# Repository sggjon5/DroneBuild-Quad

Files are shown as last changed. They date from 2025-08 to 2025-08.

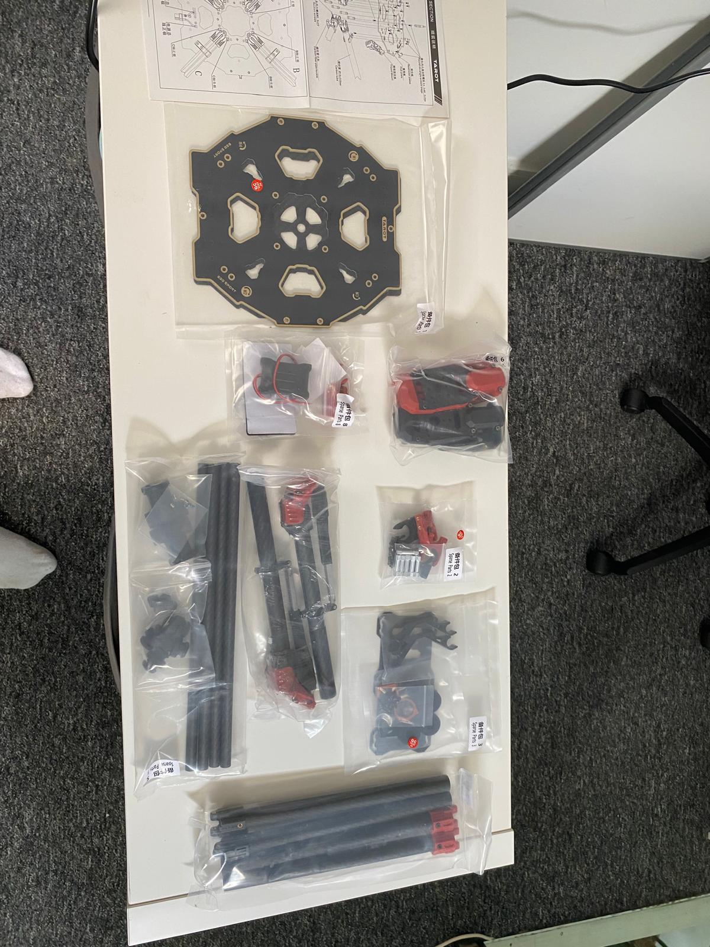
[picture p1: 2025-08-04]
media/images/frame_assembly/fame_box_component_bags.jpg

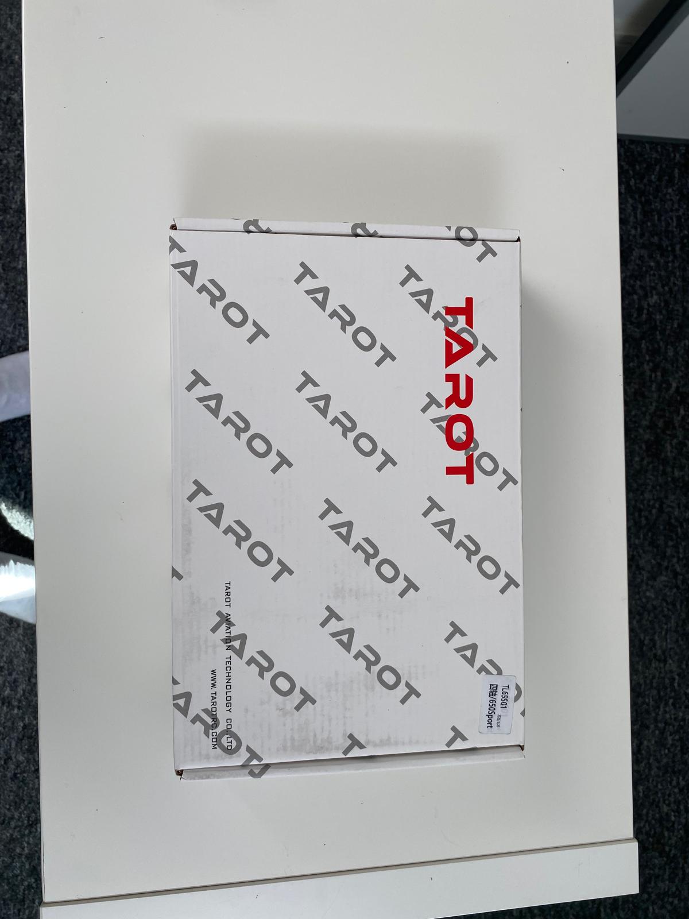
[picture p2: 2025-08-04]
media/images/frame_assembly/frame_box_closed.jpg

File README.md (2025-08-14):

# 🛠️ DroneBuild-Quad
Documenting a custom quadcopter build completed summer 2025.

hotshot

Intended to be comprehensive (but not too boring) and honest. Any questions, omissions or mistakes feel free to reach out. It has not been endorsed or sponsored by any of the products or sellers that I mention. If I have anything particular to say (good or bad) about an experience or product, it is likely included near to the section where it was utilised in the build process.

---

## 📑 Contents 

- [👋 Introduction](docs/01-introduction.md)
- [🧩Parts List](docs/02-parts-list.md)
- [🔨 Tools List](docs/02b-tools-list.md)
- [🏗️ Frame Assembly](docs/03-frame-assembly.md)
- [🪫 ESCs](docs/04-esc.md)
- [🧲 Motors](docs/05-motors.md)
- [📡 Telemetry](docs/06-telemetry.md)
- [🎮📻 Transmitter & Receiver](docs/07-transmitter-receiver.md)
- [🛰️ GPS](docs/08-gps.md)
- [💻 Software Configuration](docs/09-software-config.md)
- [✈️ Flight Testing](docs/10-flight-testing.md)

---

## 🎥 Demo Video
Please click the image below to view the drone in action. For some reasons Youtube has uploaded it as a short and I am unaware of how to change this. I am unable to upload the file to github as it is over the size limit. I have uploaded a couple of videos to a canva whiteboard that can be found [here](https://www.canva.com/design/DAGwCvz3RpU/Q3_VmZ7DQnh24HMWHGmF7A/view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). The quality should not be compressed in these

Maiden flight video (https://www.youtube.com/shorts/46lmEJWYgyI)

--- 

## 🚠 Cable/Wiring Diagram
Below is a schematic of the wiring within the quad. I feel compelled to say that it is in fact, (Not to scale).

It is an .svg file and therefore you should be able to download & zoom to read the small text notes scattered around it. 

Wiring Diagram

It does not yet include the companion computer, but I anticipate connecting this to the telem2 port of the flight controller. I have not yet decided how this will be powered.

This was made on a Canva whiteboard, as those who know me will be aware, I am a big advocate for Canva for all things presentation and design.

---

## 🤕 Mistakes

- Did not tell the vendor of the motors I was using when ordering the ESC, so had to buy a DATA LINK V2 to flash the firmware myself (~£150)
- ESCs are a bit big to run the cables through the motor arms so had to run them externally (still looks neat but less so than internal cabling) (no cost)
- Bought a wire stripper/cutter that is not very good at cutting and honestly surplus to requirements for a project of this scale... (~£25)
- Ordered the wrong XT60 pigtail (female) and soldered it to the drone, warranting either a replacement or a male to male XT60 converter (~£5)
- Did not apply threadlocker to my metal to metal connections initially (~£10)

---

## 🎉 Positive & Good Things

- The communication and fast delivery from all of the vendors (most notably 3DXR and FlyingTech) has been brilliant every time
- The soldering station is solid, does everything I would want it to and probably made my life a lot easier
- The top plate of the frame is a PDB, which I think is cool
- The battery charger did not break the bank, and it can be used as a bench DC power supply
- The build quality of the X18 transmitter feels very sturdy and good

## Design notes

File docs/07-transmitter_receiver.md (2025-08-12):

# 📻 🎮  Receiver and Transmitter 

- **Receiver** - FrSky ARCHER PLUS RS
- **Transmitter** - FrSky Tandem X18

I will provide info about the receiver, then transmitter, then the binding process and finally my configuration of mixes.

---

## 📻 Receiver
The receiver used for this build is the FrSky Archer Plus RS 2.4 GHz. This is an incredibly small and lightweight reciever weighing just over a gram. The datasheets spec it to be able to operate at >2km in good conditions and I found the whole registering and binding process very straight forward. [The datasheet](https://www.frsky-rc.com/wp-content/uploads/Downloads/Amanual/ARCHER%20PLUS%20RS%20RS%20Mini%20Manual.pdf) explains how to set up this receiever in a set of relativley short and easy steps.

The 'work' you have to do to get it ready for use is three solder joints. I used a servo cable (22 AWG) and soldered directly to the plated through holes on the board.

> [!TIP]
> Change your soldering iron tip from the gigantic one you probably used to do the ESC/PDB/Power, to a fine point one, these connections are very small.

The three connections you have to solder are as follows (colouring as a guideline only, but conforms to convention):

- Black - GND
- Red - VIN
- White - SBUS_OUT

  archer_plus_rs_pinout

 These three cables then go into a Servo connector and is connected to the "RC IN" pins on the flight controller (along the bottom edge of the orange+), with black corresponding to - and white corresponding to s.

reciever_soldered

> [!WARNING]
> **Do not stick this receiver to the frame using foam tape attached to the side with the button**. I did this and it literally pulled the button off so I had to spend 10 minutes reconstructing it with a pair of very fine tweezers to be able to bind the transmitter.

As can be seen in the above photo, the button is not actually attached anymore, this is because it was stuck to the foam tape I had used to mount it to the frame. I attached it to the top of the bottom plate when affixing it to the frame, on the back right hand side, with the antennas hanging out the side of the central body of the drone. As you can also (just about) see in the below image, the servo connector that is attached to the three cables that were soldered to the receiver, are connected to the RC IN port on the cube (furthest left rail on the bottom of the flight controller).

receiver_onboard

---

## 🎮 Transmitter

The transmitter used for this project was the FrSky Tandem X18 Dual Band transmitter. 

x18_transmitter

x18_transmitter_case

There is again, a great comprehensive video about this series of transmitters that I found useful to watch most of. I can corroborate what is said there that it does have a real quality feeling to it, even if mine is the cheapest version available.

Watch the video (https://www.youtube.com/watch?v=sJ-LwGSo7k8)

### Registration and binding process
I felt a little overwhelmed with setting this up at first but after watching the above, the menus of the ETHOS system are intuitive and pretty easy to navigate. I will add my personal selection of buttons etc below but first I will go through the binding process with the receiver.

With the reciever powered off, turn on the transmitter and follow the instructions to set up a model - it should match the configuration that you are building, in this case, a quadcopter (I think it says "multi" on the ETHOS system).

It will then suggest some channels, typically a set-up would have

- **CH1** - Roll
- **CH2** - Pitch
- **CH3** - Throttle
- **CH4** - Yaw

Once you have made this model, it should become the active model. Using the nav bar at the bottom of the screen, click on the second from the left (the plane icon) and navigate to RF system.

You then want to expand the internal module drop down and turn it on.

You should then select the protocol to be the one that matches with your receiver, in this case ACCESS.

You then need to turn on either 2.4GHz or 900M depending on what frequency your receiever operates on. As spoken through in the video, this transmitter can do both. In this case, I have turned on the 2.4GHz and left 900M turned off.

Select the Register button on the transmitter and head back over to your drone/receiver.

> [!NOTE]
> You should check your electronics for shorts before going all out with the battery for the next step. In this case, I actually used the bench power supply with 22.2V and a lower ampage (3.0A?) to safeguard against frying anything done incorrectly. I would advise to do this before plugging in a battery straight away. Check for shorts using the multi-meter etc. The battery I have came with an XT90 connector, and the pigtail I soldered onto the board was female (whereas male would have been better). Due to this, I have a succession of converters (including the powerbrick that comes with the flight controller.

Hold the button down on the reciever (you should feel it click when pressed) and plug the battery (or bench power advised) in to power on the system. The lights on the receiver should be green and red, indicating (as per the data sheet) that it is in "reg" mode.

On the screen of your transmitter, you should then see it change and the register button at the bottom of the screen should be able to be selected - click it to register the device.

After you have had a registration successful/ok message, power down the drone so the receiever is powered off.

Then, on the transmitter, click one of the three options on the same line as the regiser button (mine was RX1, RX2 and RX3) but I have seen slighly different layouts of menu's on some youtube videos.

Power the drone/receiever back on

You may have to select it on the screen of the transmitter again, but it is intutive to do and you should then recieve a bind successful message. The light on the receiver should be green and you should see the name of it (or some truncated form) in the box on the menu of the transmitter.

The above is basically a poorly worded version of the advice on the manual provided by FrSky (see the datasheet linked previously, or the image below).



The failsafe option under the RF setting I am using is no pulses.

### My Setup

This is the part I feel the most uncertain about in the entire process to be honest. I could not really find a "this is how you configure your transmitter" advice easily online, so I am going off the assumption that there are some standards but it is otherwise personal preference what the different switches etc are assigned. In anycase, here is my current mixes configuration for this quad copter setup.

| Name | Channels | Source | Notes |
|---|---|---|---|
|  Roll | CH1 | Aileron  | Default setting, what is recognised by default in Ardupilot. |
| Pitch | CH2 | Elevator | ". I had to change the weighting of this from 100% to -100% on the transmitter as the input was reversed when setting up for flight testing. |
| Yaw | CH4 | Rudder | " |
| Throttle | CH3 | Throttle | " |
| Flight Modes | CH5 | SC | Free mix - Kept as 3 position switch, will likely assign to stabilized, AltHold and RTH?. |
| RTH | CH7 | SF | Free mix - 2 position switch |

I did previously have a remote arm switch on SD on CH8, but have since removed this as I found out that holding full rudder right can arm the drone.

To change the setup of a particular switch (i.e. name, whether it is 2pos, 3pos etc), you can navigate to the settings cog along the bottom nav bar of ETHOS on the transmitter. Here you will find hardware settings > switches settings. Within this drop-down you can change the features of the switches and see what is available to you. If you are permanently renaming things, I would reccomend keeping the assigned letters in the name somwehere as it is then easy to rember which one you have assigned as arm, or kill_motors etc.

There are some things to be configured within the software setup to make some of this work but we will go through that in the next section.

➡️ [Continue to: GPS >>](08-GPS.md)

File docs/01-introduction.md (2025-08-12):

# 🛠️ Introduction

For a bit of context, I completed an MEng in Aerospace Engineering in 2021 and have since pursued a PhD with a more computer science–oriented focus, primarily exploring decision-making under uncertainty for applications in multi-target tracking. As PhDs often are, it has been heavily simulation-based, and I’ve found myself missing the hands-on challenges that come with developing physical systems, the kind that operate in the real world, not just the virtual one.

To address the above, I decided to build a quadcopter drone capable of carrying a companion computer and some onboard sensing capability (tbd), with the aim of testing some of the algorithms I’ve developed during my PhD in real-world conditions. This repository is intended to document the full lifecycle of building the quadcopter, culminating in a functional testbed for the installing the appropriate sensing hardware and the aforementioned sensor management algorithms.

The drone itself has been designed to be general purpose, with enough payload capacity to support a variety of small, but meaningful, components - making it a flexible platform for future development projects as well.

To put some numbers to it, I was aiming for a takeoff weight (without any payload) of about 2.5-3kg, with some payload capacity left over so that I could build things into/onto it in the future.

I was starting from basically no tools (other than general household things like pliers, screwdrivers, allan keys, zip-ties, etc) and have therefore included the cost of obtaining all 'new' tools in total running cost of this project to keep it transparent. As I have written this, I realised I also have a 3D printer that I used to print a GPS stand that would have likely cost ~£10 if I had not have designed and printed one.

None of this work has been sponsored by any of the vendors that I have used and therefore I am happy to provide an impartial review that they have all been excellent w.r.t. their correspondence and delivery times.

drone_portrait_outside

---

## 🎯 Project Goals

- Learn the full drone build process: from frame selection to first flight
- Create a modular and maintainable quadcopter that can be modified for other purposes
- Share a detailed, beginner friendly guide that is open and accessible

---

## 🔍 What You'll Find in This Guide

This repo contains:

- A full parts & tools list, with links and costs
- A step-by-step recollection of the process, including mistakes and things that added costs...
- A wiring diagram
- Software setup and parameters
- Demo videos and photos (from when I remembered to take them...)

Whether it is just curiosity, you are planning your own custom build, or stuck halfway through it, I hope this guide is helpful.

---

## 🧠 Skills Developed (or at least had to refresh!)

- Basic electronics & soldering
- Engineering design
- CAD (Fusion360)
- 3D printing (also had to replace the hot end on the printer)
- Firmware flashing and configuration
- Mechanical assembly
- ETHOS (transmitter OS)
- Ground control software (Mission Planner)
- Autopilot software (ArduPilot)
- Latte art
- PID tuning
- Flying a drone

➡️ [Continue to: Parts List >>](02-parts-list.md)

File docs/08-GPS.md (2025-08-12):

# 🛰️ GPS

The GPS unit being used in this build us the Here 4 that is part of the flight controller bundle purchased.

GPS

---

## Mission Planner Setup
It is pretty easy to install and use and there is plenty of documentation online. Their official documentation is [here](https://docs.cubepilot.org/user-guides/here-4/here-4-manual) and I also used this video in how to configure it within mission planner (you may want to defer this until the next step when you are doing all of the software configuration). With that said, at this point, the drone build in terms of electronics is complete and you can therefore connect to mission planner via the telemetry link and update the parameters to make it function as you desire.

Watch the video (https://www.youtube.com/watch?v=L6gyeE3Q22A)

---

## Install onto the drone
It is customary (at least historically) to place the GPS on a stand above the rest of the electronics to prevent any electromagnetic interference. I am honestly unsure how much of a requirement this is with these modern devices. Nonetheless, I thought it would give me a great excuse to get the 3D printer out and dust of my CAD skills.

> [!NOTE]
> You can buy pretty good looking, removable GPS stands from a variety of trusted vendors and they are inexpensive (~£10ish), this is not something you have to bodge yourself.

I ended up loading up Fusion360 and designing a simple stand that (due to my infrequent and lacking CAD abilities) ended up being a single piece of print, rather than as I initially intended, a modular design which I could refine and print the different elements to make better. It did however _more or less_ line up with the fixing holes available on the tarot 650 frame. 

If you do want the .stl file for it, is is [here](/files/GPS_stand_v1.stl). I will note that without reinforcing the central stick, it is quite springy, and could almost certaintly do with being thicker and shorter, or being replaced with a more appropriate material at a minimum (PLA+ be flexin). To remedy this, I quite lazily reinforced it with a wooden dowell, using two trusty zipties at the top and bottom to secure it.



I then applied some double sided sticky tape to the bottom of it and secured it in place using the two holes designed to sit over those in the top plate of the drone. Using a nut and bolt to hold the stand in place. The GPS comes with a small circle of double sided foam tape for affixing it.

GPS_installed

> [!NOTE]
> As soon as I could be bothered, I amended the CAD to make the central stick on the GPS stand thicker and considerably shorter. I then printed this [new version](/files/GPS_stand_base_v2.stl) and swapped out the old stand. I did not fix the central hole not aligning with the bolt head nearby and you still have to clip a tiny part of the plastic away.

gps_stand_v2

➡️ [Continue to: Software Setup >>](09-software-config.md)

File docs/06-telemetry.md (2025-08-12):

# 📡 Telemetry
The telemetry selected for this build was the RFDesigns 868x-EU radio bundle. 

> [!NOTE]
> You will likely have to buy the cable that goes from the telemetry unit to the telemetry port on the flight controller seperatley.

The setting up of these components was actually very simple. As I had purchased a pair as a bundle, they had already been programmed to have the same settings and find eachother. I did find a brilliant video that spoke all about them and was worth the watch in its entirety to understand. I will link it below.

Watch the video (https://www.youtube.com/watch?v=lN28v68aL_Y)

This video talks you through everything I would type here and is much easier to scrub through and find the parts you need/want. Most notably, the checking that all the parameters are aligned on both your radios and how to actually plug them in and check it is all working.

I will however mention how you actually orientate the connector onto the pins (it is also convered in the video). Your connector will have a little arrow in the top corner above the (most likely) black cable.

telemetry_cable

This arrow goes onto the far left, bottom rail of the RFD868x-EU pins (there is likely a plastic blocker stopping you from using the top rail).

telemetry_nearly_plugged_in

telemetry_plugged_in

To state the obvious, one of the telemetry modules goes onto the drone and one goes into your computer (via the USB cable provided in the bundle).

I attached the one on the drone to the underside of the main body, using a piece of 3M foam tape and threaded the cables through the holes in the lower and top plate to plug it into my telem1 port on the cube pilot.

telem_on_drone

After taping this on, it became apparent that the front panel of the module was just a push fit casing. Prior to the first flight I added a small ziptie around the module, threaded through the nearest hole on the bottom plate of the central drone body.

It is reccomended online that you make a seperate power source for the radio but given the fact that the RFD868x-EU operates at 5V and has a "~800mA max peak (at maximum transmit power)", it can quite comfortably be powered by the telem1 port on the cube orange plus as this also operates at 5V and can provide up to 1.5A [link](https://discuss.cubepilot.org/t/serial-port-problems/5654/5).

➡️ [Continue to: Transmitter & Receiver >>](07-transmitter_receiver.md)

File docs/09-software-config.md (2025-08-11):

# 💻 Software Configuration

For this build I am using Ardupilot and mission planner. The setup process is well guided and there is plenty of good documentation online for this. 

The things I would highlight though are:

- You do not need to calibrate the Alpha ESC's from what I can find online
- You need to fix your Flight controller and GPS in place to do the calibrations
- **Do not put the propellors on for any of the testing**
- Check, check and check again that your motors are spinning in the right direction that is expected by the software

## 📶 Connecting Mission Planner

To connect mission planner to your drone, we will use the telemetry setup that we have established. Plug the second (i.e. the one not on the drone) telemetry module (with antenna screwed on) into your PC using the USB cable provided in the bundle. Then, power on your drone. Whilst doing this, you can also turn on your transmitter and allow it to automatically connect to the receiver on the drone (as we have set up the binding and registration earlier) using the model that was setup previously.

>  [!WARNING]
> Do not do this if you have props attached. Remove all props before any power is connected to your drone.

On the successful connection of your telemetry modules (indicated by a solid green and flashing orange light), navigate to the top right corner of mission planner (can be downloaded [here](https://ardupilot.org/planner/docs/mission-planner-installation.html)) and select the first drop down box. There should be a COMX option available. For example, mine is COM6. The Baud rate for my setup is 57600 but it may differ for different arrangements. Click connect in the top right corner.

A "Getting Params" pop up box will then appear and begin to load as it connects to your drone via the telemetry link we have established - this may take a moment.

---

## 🗺️ Mission Planner Setup

The main steps you want to take are under the setup cog on the top navigation bar. Working your way through the side panel on this tab is a good starting point. The documentation and community surrounding ardupilot and mission planner is very strong and usually any errors can be resolved by googling them and navigating to one of the easy to find forums. Most of the errors you will encounter have likely been seen before.

The other things to remember here are:

- The setup of the GPS through the CAN port, if you skipped this step earlier, now is the time to do it
- The above GPS setup includes the disabling of the safety parameter, as there is no safety switch installed onto this aircraft (yet!)
- On Initial tune parameters, the screw siize relates to the size of the prop in inches, in this case it is 15. The battery cell count is 6 and it is a LiPo Battery. You will need to change these according to your setup.
- I found on a blog reply that under ESC calibration (or via the full parameters list) the PWM min for these ESCs should be set to 1100, and the PWM max should be set to 1940. You also (according to the same blog) do not need to calibrate the Alpha series of ESCs.

---

## ✈️ Flight Modes

Under the flight modes tab you will see 6 flight modes available. The way to check which of the flight modes are mapped to your CH5 3-position switch (that we setup in the transmitter mixes), is to simply change the position of that switch (in this case SC) and see the highlighted flight mode change. The three modes I have selected are stabilize (SC up), Alt Hold (SC centre) and Return to Land (RTL) (SC Down).





Once you have completed all of the orientations/calibrations etc you can then get something moving - the motor test!

---

## 🧲 Motor Test

I know I have said it before, but I will say it again just in case.

> [!WARNING]
> Remove all propellors before doing the motor test.

Navigate to the optional hardware dropdown in the sidebar of the setup tab and select motor test. Here you can diligently check that the motors are spinning in the right direction. An easy way to test this is to rip a strip of paper and hold it against the motor as it spins for the 2 seconds at 5% throttle. This gives a clear indication of which way the motor is spinning and you can ensure that it matches the setup shown in the software that is required.

> [!NOTE]
> The stickers that come as a defualt on many frames do not necessarily match the numbering in the mission planner software. Check this carefully to ensure what is happening in the real world is what is expected to happen, governed by the labelling in the software.

If the motors are not spinnning, it could be that the signal cables are not correctly assigned/oriented, it could also be that there is not enough power to spin the motors (if you are still attached to a low amp bench power supply, for example) or it could be that the connection between the ESC and the motor is faulty.

One sign that the connections are correct is that when you power on the drone, you should hear a succession of around 5 beeps, proceeded by one longer beep. This is also dependent on turning off the safety parameter we mentioned in the GPS setup section. The noises made by the ESC can be decoded and often have some meaning. I have not had to go through this but a google of what the beeps mean for your specific ESCs should turn up some results and information to then act on.

 ---
 
## 🦾 Setting a Remote Arm Switch

> [!NOTE]
> This is something I set up at first but have since removed as you can remotely arm the controller by holding the left hand stick all the way down and right on the transmitter. I have left the below in but since learning of the stick arming, I would reccomend removing the arm switch from the transmitter.

I know I have said it before, but I will say it again and again just in case.

> [!WARNING]
> Remove all propellors.

Now you have confirmed everything is working as anticipated, we can set the arm switch we assigned to channel 8 on our transmitter to actually mean something to the drone via changing some parameters in mission planner. The video linked below goes through the whole process but I will highlight the key details (I would still reccomend watching the video, it is very short and straight to the point).

- Go to config > full parameter list
- Search for rcX_option, where X is the number of the channel you have assigned to be your arming channel (in this case RC8_OPTION)
- Change the value to 153
- Write the parameter changes back to the flight controller (button on right hand menu)

It is worth noting that you can also do this through the Extended tuning menu by setting the corresponding RC Opt to be ArmDisarm.

Watch the video (https://www.youtube.com/watch?v=wtwehddboB4)

---

## 🛸 Fake Flying

Okay, now everything is working as expected, the motors are spinning safely in the correct direction and we have a way to arm the drone for flight.

> [!WARNING]
> Remove all propellors.

We can now pretend to fly the drone and test the responsiveness of the control input and validate that it is making a difference to the actual physical system.

- Ensure the throttle is all the way down, the drone is in stablize mode and the throttle cut is not active
- Arm the drone (holding rudder down and right)
- The artificial horizon on the data tab of mission planner should change to say ARMED
- The motors will start spinning
- If all sounds good, start to slowly increase the throttle to 50%
- Then, once this has settled, start to move the right stick around and hear the motors change and modulate to what you are doing
- Then, bring the throttle down to idle, disarm the drone (rudder full left) and compelte the test

- An alternative is to pick up the drone in stabilise mode and perturb it from its horizontal state, the stabilize mode should react to your actions and you should hear this reflected in the motors movement

Watch the video of this motor test by clicking on the image below.

[(drone_portrait_outside)](https://www.youtube.com/watch?v=z5--iK6VvRA)

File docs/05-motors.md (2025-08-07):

# 🧲 Motors

The motors selected for this project were the T-motor MN4014 330KV motors - a member of the navigator series.

MN414_motor_up_close

According to the manufacturers datasheet, these motors (when paired with the selected propellors) will provide 830g of thrust at 50% throttle, meaning a total thrust of 3320g. 

By making some assumptions[^1] we can ascertain the relationship between % throttle and thrust to be y = 22.517x - 284.79. Which then provides:

- at 40% throttle, 4 x 615g = 2460g
- at 45% throttle, 4 x 728g = 2912g

This provides the confidence that we will be able to hover (where weight=lift) at an appropriate throttle setting (aiming for between 40-50%) to give good control authority (mass of the drone is currently predicted to be 2,839.3g).

The other consideration with motors (beyond their physical size and if they will fit) is the voltage that they operate at. This information can be obtained from their data sheet and can be deciphered with the knowledge that there is nominally 3.7V per cell. So if the motor claims an operating voltage of 22.2V, this means it is suited to a 6S battery (as 6 * 3.7V = 22.2V). As a realted note, LiPo batteries are considered to be fully charged at 4.2V and fully discharged at 3.0V. It is common practive to stop flying between 3.4-3.5V to preserve the battery and store the batteries at a balanced 3.8V per cell.

The numbers within a motors name typically conform to the convention of stator diameter by stator height - so in this case, these motors are 40mm i diameter and 14mm in height, forming the 4014.
)
The KV rating is an indicator of speed potential. It describes the revolutions per minute (RPM) a motor will achieve per Volt that is put into it. Typically, higher Kv motors spin faster and have lower torque and the opposite is true of lower Kv rated motors. There is plenty of literature online about this sort of thing and it is not my area of expertise so I shall defer you to other, readily available resources online if you want to do any further reading around this.

[^1]: the assumptions are that the relationship is _almost_ linear between % throttle and thrust provided by the motor, verified by plotting some of their similar motor data that includes a lower range of throttle percentage data points. Using this info, a simple linear regression can be applied to the motor data on this motors datasheet.

---

## Shortening the cable length 

The one thing that did surprise me is that the length of the cables that came as standard on the motors was 50cm - lending itself to placing the ESC in the main body of the frame; or have a large bundle of cables at the end of the arm. This led me to reconsider whether the setup I had already selected (ESCs under motors) was the optimal architecture. 

MN4014_motor_full_cable_50cm

Mainly driven by not wanting bunches of cables strapped to my (already arguably too big) ESCs, I did some reading around shortening the cables of the motor. The internet left me feeling like the answer was yes, but ensure the cables remain the same length otherwise there will be marginal differences going between the phases of the motor caused by differences in length of the cables. I corroborated this finding with someone in the know and confirmed that I would be okay to shorten the cables.

> [!IMPORTANT]
> If you are shortening the length of the motor cables, make sure you keep them the same length, as varying length may imbalance the motor.

I decided to shorten them enough so that there was not a lot of excess cable there, but left them long enough such that I could use a thicker zipclip around the motor mount clamps to both reinforce the clamping and also hold the ESC -> motor cables in place. I also wanted to use the original connectors that came on each motor, rather than retrofitting my own. To make sure all of these criteria were met, I shortened the length from 500mm per cable to a total of 235mm per cable. I did this by first cutting the length from motor to cable end to 175mm, and then cutting off the connector from the end of the stray cable to a length of 60mm. I then soldered these two parts together, effectivley reattaching the male bullet connector at shorter lenth.

> [!TIP]
> Make sure you put the heat shrink tubing on the cable before you reattach the connector!

motor_cable_shotening_in_progress
motor_shotened_cable3

---

## Installing the motors onto the motor mounts
The motor mounts have a carbon plate on their top side which fixes to the motors via a selection of holes within it. It is highly likely that some of these will align with the mounting holes on the bottom of your motor. I used four screws per motor to mount them to the carbon plate.

carbon_motor_mount_plate

An important observation that was made during this build was that the mounting screws included with the motor were (just!) too long and impeded the movement of the motor by making contact with the coils. This was due to the fact that the mounting plate is a thin carbon fibre element, if it were bulkier then this would not be an issue. To me, there were two options:

- Replace the M3 bolts with shorter versions
- Use washers on the outside of the mount

As I had some shorter bolts (8mm?), I used these.

The screws that came with the motor (I think 12mm)
old_motor_screws

The photo I took when changing the screws.
changing_motor_screws

Once I had changed all of the screws over I then re-mounted all of the motors to the frame. The ordering of the cables from the ESC to the motor was not important at this point as I would determine their spin direction later on when configuring the software. In the interim, I just connected all four motors the same with the cables going to their nearest connector as shown below.

ESC_connected_to_motor_closeup

(ultimatley you will end up swapping over the 2 of the 3 cables on two of the motors to get them to spion in the correct direction, but as they are now attached via bullet connectors, this is an easy and fast process.)

drone_assembled_propulsion_installed3

---

## Props

The props being used in this build as the Carbon P15x5 props recommended by T-motor to pair with the MN4014 motor being used. It is important to check that the frame you are using/have designed has enough clearance for the size of the props you want to use. Ideally you would not have the props effectivley being tip to tip when they are spinning, there should be a safe amount of cleareance between them at all points of their rotation.

The props should not be installed at this point as you will just have to uninstall them as soon as you connect any power. But it seems appropriate here to discuss the them. 

With the t-motor props, they are sold in pairs, often one being a clockwise (CW) prop and one being a counter clockwise (CCW) prop. This is conventially declared from a top down view of the drone w.r.t. which way they spin.

The coding on the propellors here are the markings L and R. With 

- L meaning clockwise
- R meaning counter-clockwise

You can find this lettering on the topside of each propeller.

propellors

Both the motors and the props likely came with small discs which sit on top of them and the bolts go through when installed, I used the ones from the motor box but the two sets were the same diameter, shape and thickness. They come with a card that explains the installation. 

> [!NOTE]
> There is also little coloured stickers with the props that can be used to pair a prop with a particular arm/motor. I would advise checking the rotations are correct multiple times before changing your reference point to the stickers!

➡️ [Continue to: Telemetry >>](06-telemetry.md)

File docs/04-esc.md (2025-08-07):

# 🪫ESC (no ESC emoji)

The ESCs that I selected were the T-Motor Alpha 60A, as they were the most appropriate that were available from where I was ordering the bulk of the components from.

ESC_in_box

> [!IMPORTANT]
> I should note that if you are going to use the t-motor alpha series, you need to put the corresponding firmware onto them, using a DATALINK V2 (~£150).

3DXR offer to do this for you if you leave them a note of which motor you are planning on using. You also need to check the t-motor website for which ESC is compatable with which motor. The motor I have (MN4014) is not paired with this ESC. In the interim I have flashed the firmware of the motor that _is_ available that is closest in size and KV rating. The listed motors available on the ESCs I have are

motors_available_on_ESC

I did however reach out to t-motor and they have promised to write some custom firmware (within 3-4 weeks) to pair this ESC with this motor, which if it happens, is excellent customer service as the error is entirely my fault. As far as I understand it, the incorrect firmware will not prevent the motor from working as any ESC _should_ be able to make any motor work (subject to current draw limitations). I believe it is a case of if the firmware is incorrect, the motor is not running at its optimal efficiency - but again, this is not my area of expertise and is what I have concluded from my fragmented scouring of the limited information I could find online.

The recommended pairings for the motors and ESCs can be found [here](https://store.tmotor.com/article.php?id=249&srsltid=AfmBOopyixdGDCuPRMzZdIhsSHbEJ-VuuUXD7wQcLlyIUUaO3qEwRVjc).

---

## Using T-Motor software and DATALINK V2 to flash firmware of motor
As mentioned above, you need to flash the firmware for your motor with the Alpha series of ESCs, using a DATALINK V2 and their software suite. A good video on how to compelte this process is here:

Watch the video (https://www.youtube.com/watch?v=-yPCoabfOz0)

Things to watch out for:

- You need to be able to power the ESC to do this
- The sequence of when you plug things in/power things on/click buttons in their software is important, follow the video carefully.
- The software for the DATA LINK V2 can be downloaded from [here](https://uav-en.tmotor.com/2018/alpha_0502/158.html)

---

## Installing the ESCs

This process is covered in sufficient detail in the video linked on the frame assembly page, but (typically) you have two options:

- Install under the motor mounts
- Install within the main body of the drone

Within this setup, despite their larger size, I chose to install them them under the motor mounts. Because of this, the power cables on each ESC required extending. 

### Extending ESC power cables
As described above, the length of the preinstalled wires on the ESC were not long enough to reach from where they were to be installed to the centre of the frame where the soldering points are on the PDB. They therefore were extended by a short length (shown in the photos) using the 14AWG silicon wire.

Alpha 60A 6S ESC

ESC_to_PDB_cable_extension

ESC_extension_not_soldered

ESC_extension_soldered

This was everything laid out on the storage table before I started attaching connectors

motor_top_plate_electronics_laid_out_ESC_cables_motors_on2

### Soldering Bullet Connectors onto the ESC
At this point it is worth considering how you wish your ESC and motors to be connected. Many motors come with connectors already installed on the end of their cables - it is worth finding out what connectors are on the end of the motors you have selected. In this case, the MN4014 came with 3.5mm bullet connectors on the end of them. This is not to say that it cannot be changed, or that you could not just remove them and solder the cables directly, but bullet connectors are a common choice for connecting your ESC to your motor.

motor_male_bullet_connectors

As the connectors on the motor are male, we needed to install female connectors of the same size onto the ESC cables.

> [!TIP]
> Use a set of helping hands for this, the connector conducts heat very well as it is lilely fully metal, and it can therefore get very hot...

helping hand_holding_bullet_connector2
helping_hand_holding_bullet_connector

> [!TIP]
> Put the heat shrink onto the cable before you solder the connector on.

ESC_next_to_installed_motor

### Installing the ESC's onto the frame and cabling

Due to their larger size, there was an issue with running the ESC cables through the arms of the drone as shown in the assembly video, meaning I had to route them down the arms, along the underside, using zipties to keep them in place. 

A single thicker ziptie was also used to hold the ESC in place, threading through the motor mount and *not* threading through the carbon plate on which the motor will be fixed to. This means you need to remove the screws and carbon plate on the topside of each motor mount to thread the ziptie.

One thing to note is that whilst ziptieing the cables down onto the arms, I made sure there was still enough freedom in the ends of the cables so that I could manouvre them easily enough as the next step would be to solder the ends down.

> [!NOTE]
> These photos were taken after the final assembly had been complete so please do not feel as through you have missed steps w.r.t. other cabling and components you may see.
>
> Most notably, the ESC to motor connection cables were not ziptied underneath at this point as the motor cables had not yet been shortened.

under_arm_cables
drone_underside_showing_cable_management

Once you have installed the ESC and are happy with its cabling, you can then solder the power cables to the PDB contact points. Make sure the polarity is correct (Red +, Black -). If you are not familiar with soldering, it is worthwhile watching a few youtube videos on how to do it neatly and effectvley. I would also reccomend having a go at doing it on non-critical/spare components first (i.e. two cables together, cable to connector etc). You can buy practice boards but my advice here would be to make sure you buy one that is appropriate for what you are doing - there is little point in buying a super tiny one if you need practice at soldering thick large cables. 

> [!TIP]
Solder flows to the hot area, the idea is to heat up what you are adding solder to and then melting the solder so it flows to it. Thinking of it this way will likely negate many of the early frustrations of things not sticking.

Another one would be

> [!TIP]
If you are new to it, do not be lazy, change the solder tip to an appropriate one. If it is a big joint, then use a big soldering iron tip.

As I am writing this I think it may be worth putting into a different standalone section but I will leave it here for the time being.

### ESC Signal Cables

The final connection that needs to be made is the ESC signal cables being plugged into the corresponding pins on the bottom rail of the cube orange+ flight controller. This does not need to be done immediatley but your cable management plan should include it. The airframe setup section of your selected software will provide you with the mapping of which motor goes to which pin. At this point, I put a loose ziptie around all of the cables and left them bunched in the central hole of the top plate. This allowed them to stay together and not get tangled until I was ready to figure out where they were going. You can just about see the bunch of connectors coming through the top central hole on the drone in the below image.

drone_assembled_propulsion_installed3

One thing that is worth noting is that with these Alpha ESCs, there are two, three-pin connectors that come out from them (along with another single connector wire).

- The three pin connector with all three cables attached are for flasing the correct firmware to the ESC
- The three pin connector with **only two** cables attached are the ones we want to connect to the rail on the flight controller.

If you connect the three cabled version, when you come to test your motors, nothing will happen (I can speak to this from experience...)

So to summarise, at this point the frame is assembled into its primary sections, the ESCs have been mounted under the motor mounts, cables have been extended and relevant connectors attached and the ESC power cables have been soldered onto the PDB.

➡️ [Continue to: Motors >>](05-motors.md)

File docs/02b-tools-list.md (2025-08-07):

# 🔨 Tools List
A table of everything I purchased for this build. You could get away with buying cheaper versions of many of these items but I have often put some time into researching which items are well reviewed/recommended by reputable sources before purchasing any larger items.

| Category | Component | Supplier / Link | Price (£) | Notes |
|---|---|---|---|---|
| **LiPo Safety Bag** | GensAce LiPO Safe Bag | [3DXR](https://www.3dxr.co.uk/electronics-c78/chargers-c74/gensace-gens-ace-lipo-safe-bag-p5557) | £9.99 | Cheaper ones were not in stock, this one is the same shape as the battery though which is nice.  |
| **LiPo Charger / DC Power Supply** | SkyRC S100 neo AC 100W / DC 200W 1-6S Battery Charger | [FlyingTech](https://www.flyingtech.co.uk/product/skyrc-s100-neo-battery-charger/) | £44.99 | So far this is great, wanted one that can be used as a DC supply so that I can use as a bench power for testing when building. Not sure how common this is with chargers but this one was well reviewed and not that expensive. It does not feel like a gigantic fire hazard! Also small enough that you could take it into the field when flying to assess battery status! A great allrounder. |
| **LiPo Charger to Croc Clips Lead** | XT60 Female to Croc Clips Cable | [FlyingTech](https://www.flyingtech.co.uk/product/charge-lead-adapter-xt60-female-to-crocodile-clips/) | £4.80 | So I could use the charger as a bench power supply.  |
| **Multimeter** | Digital Multimeter | [FlyingTech](https://www.flyingtech.co.uk/product/chy-a830l-digital-multimeter-w-backlit-display/) | £12.00 | Cheap and feels it, but serves its purpose for continutity checking.  |
| **Wire Strippers** | Self Adjusting wire strippers and cutter | [FlyingTech](https://www.flyingtech.co.uk/product/self-adjusting-automatic-insulation-stripper-wire-cutter-32-7awg/) | £22.99 | Did not need these, did most of the stripping with a stanely knife and also the cutter on these is terrible - gets jammed shut and you have to wiggle the cable. Better off using a pair of snips.  |
| **Solder** | TBS Solder 100g, 0.8mm diameter | [3DXR](https://www.3dxr.co.uk/building-c23/tools-c170/team-black-sheep-tbs-solder-100g-p5484) | £7.95 | Wanted some nicer solder than what came with the soldering station, this had good reviews, bundled it in with another order.  |
| **Velcro Tape** | Hook & Loop Vectro Tape 50mm width (Industrial Strength) | [3DXR](https://www.3dxr.co.uk/building-c23/tapes-c130/velcro-c350/3dxr-hook-loop-velcro-tape-industrial-strength-ps51-ps52-per-metre-p5425) | 2 x £4.00 = £8.00 | Sold by the metre.  |
| **Soldering Station** | YIHUA 938BD+ Soldering Iron Station & Hot air rework station | [Amazon](https://www.amazon.co.uk/dp/B08YD8JQHX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) | £89.99 | Recommended by [Tom's Hadware 2025](https://www.tomshardware.com/best-picks/best-soldering-irons), so far it has been great, heats up quickly, lots of different end effectors (or whatever they are actually called) has a sleep mode and the hot air functionality is also super handy.  |
| **Soldering Mat** | yowtiny Soldering Mat Large - Silicon | [Amazon](https://www.amazon.co.uk/dp/B09QGV8XP9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) | £11.99 | Great, saves me burning holes in things and ruining surfaces as I am doing all of this in a domestic setting, as opposed to a workshop. |
| **Heat Shrink Tubing** | ASHINER Heat Shrink Tubing (580 pcs) | [Amazon](https://www.amazon.co.uk/dp/B08XXGNJHG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) | £8.99 | Required for protecting soldered joints of cable-cable and also cable-connector. |
| |  |  | | | 
| **Tools Totals** | | | **£221.69** |  |

Resulting in the total running cost of the project to be **£2631.64** (+ £162.84 mistakes).

➡️ [Continue to: Frame Assembly >>](03-frame-assembly.md)

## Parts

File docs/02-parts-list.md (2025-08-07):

# 🧩 Parts List

Below is a complete list of the components used to build the quadcopter, including the prices at the time of purchase and links to suppliers where available. I have also included some notes on why certain components were selected and any alternatives that were (more seriously) considered. Everything in the table below I would consider as necessary (or at least some equivalent required) to make the drone functional. Between this and the [tools list](02b-tools-list.md), there were not many things I would say are entirely surplus to requirement.

| Category | Component | Supplier / Link | Price (£) | Mass (g) | Notes |
|---|---|---|---|---|---|
| **Frame** | Tarot 650 Sport | [FlyingTech](https://www.flyingtech.co.uk/product/tarot-650-sport-carbon-fibre-foldable-quadcopter-frame/) | £149.90  | 750g  | 600mm wheelbase, carbon fibre, top plate is the Power Distribution Board (PDB), ideal size for carrying the payloads anticipated.  |
| **Motors** | T-Motor MN 4014 330KV | [3DXR](https://www.3dxr.co.uk/multirotor-c3/multirotor-motors-c35/t-motor-mn4014-p3510) | 4 x £96.90  = £387.60 | 4 x 160g = 640g | Provide sufficient thrust for anticipated mass of quad, slightly overspecified but this will allow slightly larger battery and also more opportunity for alternative payload. Provide 830g of thrust with recommended props (selected below) at 50% throttle. Also operate on 6S battery voltage. |
| **ESCs** | T-Motor Alpha 60A ESC - 6S | [3DXR](https://www.3dxr.co.uk/multirotor-c3/multirotor-escs-c48/t-motor-alpha-60a-6s-lv-p2888) | 4 x £69.99 = £279.96 | 4 x 63g = 252g  | Slight mistake made here, recommended alpha esc for the selected motor is the 40A version of this esc, also did not tell 3DXR as they were in seperate orders and had to buy the datalink v2 to flash the firmware myself. |
| **Flight Controller & GPS Bundle** | The Cube Orange+ Standard Set & Here 4 GPS | [3DXR](https://www.3dxr.co.uk/autopilots-c2/the-cube-aka-pixhawk-2-1-c9/cube-autopilot-and-combos-c10/cubepilot-bundle-the-cube-orange-standard-set-hx4-06222-here-4-hx4-062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) | £600.00 | 133g | Lots of functionality, compatible with ardupilot, could easily be re-purposed for another use case. |
| **Propellers**  | T-Motor Carbon Prop P15x5 | [3DXR](https://www.3dxr.co.uk/multirotor-c3/multirotor-props-c265/t-motor-carbon-prop-p15x5-p2789) | 2 x £55.90 = £111.80  | 4 x 21g = 84g |  Priced per pair, need four in total. Reccommended props from T-Motor for selected motor pairing. |
| **Telemetry** | RFDesign 868x - EU Radio Modem (UK & Europe Bundle) | [3DXR](https://www.3dxr.co.uk/radio-gear-c33/telemetry-c31/868-mhz-telemetry-c65/rf-design-rfdesign-rfd-868x-eu-radio-modem-uk-and-europe-bundle-p4243/s4671) | £280.00  | 15g  | UK compliant, long range >40km, well documented and usable software suite. |
| **Telemetry Cable** | RFDesign Pixhawk 2 to RFD900/868 Telemetry Cable | [3DXR](https://www.3dxr.co.uk/radio-gear-c33/telemetry-c31/telemetry-cables-accessories-c465/rf-design-rfdesign-pixhawk-2-to-rfd900-868-telemetry-cable-p5415) | £5.95 | 2g | Telemetry cable required to connect the RFD 868x-EU to the flight controller. |
| **Receiver** | FrSky Archer PLUS RS 2.4GHz (OTA ACCESS) | [3DXR](https://www.3dxr.co.uk/radio-gear-c33/receivers-c112/frsky-archer-plus-rs-2-4ghz-receiver-ota-access-p4556/s5005) | £21.50  | 1.3g  | Very small, easy to incorporate into frame, ACCESS compatable and claimed range of ≥2km. |
| **Transmitter** | FrSky Tandem X18 Dual Band 900m/2.4GHz Radio | [FlyingTech](https://www.flyingtech.co.uk/product/frsky-tandem-x18-x18s-x18se-dual-band-900m-2-4ghz-radio/) | £267.90  | NOT ON DRONE  | Well reviewed, compatable with ACCESS reciever, runs ETHOS which is also well reviewed. |
| **Battery** | GensAce Tattu 7000 mAh 25C 6S1P 22.2V LiPo | [3DXR](https://www.3dxr.co.uk/electronics-c78/batteries-c144/gensace-gens-ace-tattu-7000mah-25c-6s1p-22-2v-lipo-with-xt90-p3644) | £132.90  | 812g  | 6S compatable with motors, battery size compatable with frame, with the selected props, 3.6A @ 50% throttle so *4 = 14.4A (roughly at hover), giving approximate flight time of 30 minutes. |
| **Onboard Computer** | Raspberry Pi 5 16GB | [The Pi Hut](https://thepihut.com/products/raspberry-pi-5-starter-kit?variant=53972414693761) | £147.00  | 100g  | Will be used for running onboard algorithms. |
| **Battery Connection Converter** | XT60 to XT90 Plug adapter | [FlyingTech](https://www.flyingtech.co.uk/product/xt60-to-xt90-plug-adapter/) | £3.90  | -  | Battery comes with an XT90. I initially ordered the wrong one of these and had to order another (see table below). The one i actuall;y wanted was XT60 Female to XT90 Male.|
| **Battery to PDB (pigtail)** | XT60 10cm Pigtail connector | [FlyingTech](https://www.flyingtech.co.uk/product/xt30-xt60-xt90-male-female-10cm-wired-pigtail-connectors/) | £1.90 | -  | I ordered a female one, if I was going to do it again, I would order a male one and flip some of the connections round. |
| **Power Cabling** | Amass AWG Silicone Wire 14 AWG Black | [3DXR](https://www.3dxr.co.uk/electronics-c78/cable-wire-c295/amass-awg-silicone-wire-cable-p5271) | 2 x £0.95 = £1.89 | -  | Sold by the metre. Needed to extend ESC cables to reach from under motor mounts to soldering points on PDB (top plate) of drone. |
| **Power Cabling** | Amass AWG Silicone Wire 14 AWG Red | [3DXR](https://www.3dxr.co.uk/electronics-c78/cable-wire-c295/amass-awg-silicone-wire-cable-p5271)  | 2 x £0.95 = £1.89  | - | Sold by the metre. Needed to extend ESC cables to reach from under motor mounts to soldering points on PDB (top plate) of drone. |
| **Servo Cable** | Amass Servo Wire 22 AWG (Twisted) | [3DXR](https://www.3dxr.co.uk/electronics-c78/cable-wire-c295/servo-extensions-c157/amass-servo-wire-22-awg-twisted-per-meter-p4776) | 2 x £1.25 = £2.50 | -  | Sold by the metre. Overordered incase of mistakes. Needed it to solder to reciever at appropriate length. |
| **Bullet Connectors** | Amass SH3.5mm Bullet Connectors (10 pairs) | [3DXR](https://www.3dxr.co.uk/electronics-c78/connectors-c107/amass-sh3-5-3-5mm-bullet-connectors-10-pairs-p4190) | 2 x £4.75 = £9.50 | -  | Wanted to use them to connect motors to ESCs rather than direct soldering. |
| **Servo Extension Cables** | Male to Female Futaba Connector Servo Cables (10cm) | [eBay](https://www.ebay.co.uk/itm/193481616595?var=493692361048)  | £5.75 | -| Sold in packs of 5. Used to extend ESC signal cables to reach flight controller, and also reciever. |
| |  |  | | | |
| **Totals** | | | **£2409.95** | **2,839.3g** |  |

I have bundled all of the 'cabling and connectors' into a conservative 50g estimate when doing the mass calcualtions. Meaning that I am currently working to a total mass of **~2.839kg** and a total cost (without tooling and mistakes) of **£2409.95**.
 
---

## Items Due to Mistakes
Then the things I 'had' to order after the fact because of some sort of mistake on my end...

| Category | Component | Supplier / Link | Price (£) | Mass (g) | Notes |
|---|---|---|---|---|---|
| **For ESCs** | T-Motor DataLink V2 | [3DXR](https://www.3dxr.co.uk/multirotor-c3/multirotor-escs-c48/t-motor-alpha-data-link-v2-p2899) | £154.99  | NOT ON DRONE  | Probably (and hopefully!) the most expensive mistake I made. I did not read the literal red text at the bottom of the ESC's description (or I did but then completley forgot when ordering), so had to buy this bit of hardware such that I could program the ESCs to match the motors. More about this later...  |
| **Battery Connection Converter (wrong one)** | XT60 to XT90 Plug adapter | [FlyingTech](https://www.flyingtech.co.uk/product/xt60-to-xt90-plug-adapter/) | £3.90  | - | I initially ordered a XT60 Male to XT90 Female which was the wrong way round for my setup... |
| **Battery Connection Converter (due to bad planning)** | XT60 Male to XT60 Male adapter | [eBay](https://www.ebay.co.uk/itm/256806148373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) | £3.95  | -  | Due to my evident poor planning of connector availability and the fact that I jumped the gun and already soldered the pigtail to the PDB, I decided it would be easier to just get a converter to make it work rather than changing the pigtail for a male ended XT60. |
| |  |  | | | |
| **Totals (incl. mistakes)** | | | **£2572.79** | **2,839.3g** |  |

So now, including the fact that I did not request the ESC's to be programmed to my motors, the running total is **£2572.79**. Herein, I will delcare the running total as a price + mistakes. 

➡️ [Continue to: Tools List >>](02b-tools-list.md)

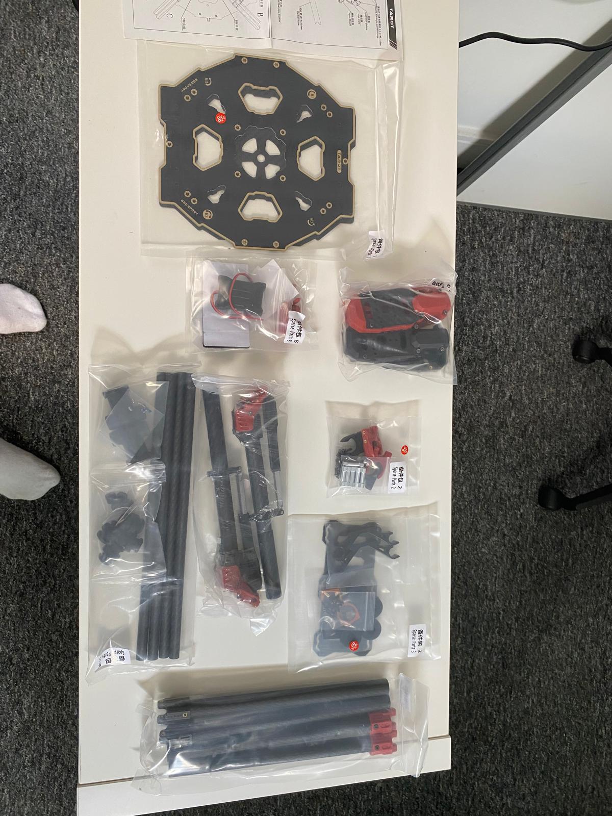
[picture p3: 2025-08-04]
media/images/frame_assembly/frame_box_component_bags2.jpg

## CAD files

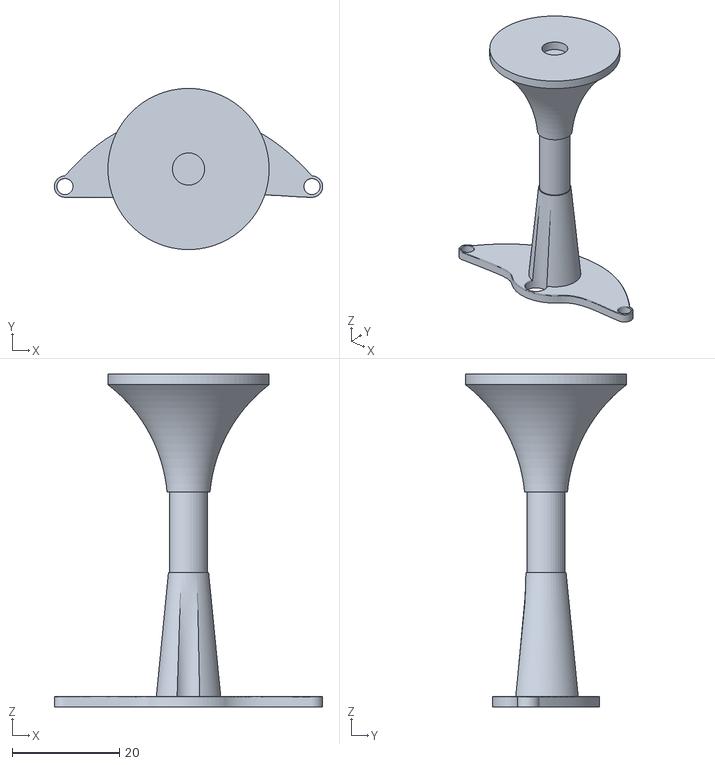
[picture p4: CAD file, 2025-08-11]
files/GPS_stand_base_v2.stl
50.0 x 30.0 x 62.0

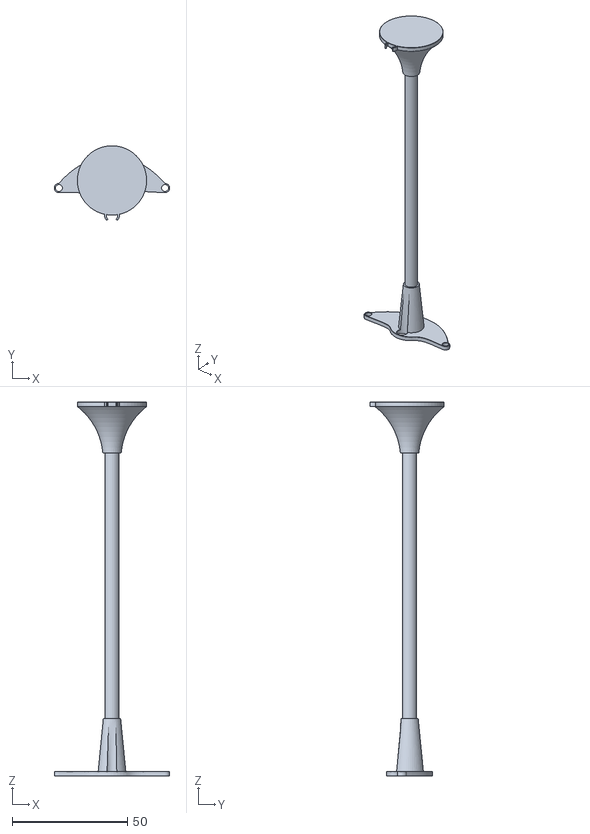
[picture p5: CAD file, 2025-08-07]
files/GPS_stand_v1.stl
50.0 x 32.2 x 162.0

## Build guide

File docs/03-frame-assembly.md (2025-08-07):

# 🏗️ Frame Assembly

The frame selected was the Tarot 650 sport. The primary reasons were the size and weight and the fact that the top plate is actually a power distribution board (which I think is pretty cool). The retractable landing gear is a nice feature that is included but this was not really a major factor in the decision. Maybe I will come to love this if I install a camera onto it...

The frame comes neatly packaged in a Tarot box and is quite easy to put together. The screws are pretty small so my advice (as with pretty much all of this process) would be to set up the area you are working in so that it is difficult to drop and lose them. With that said, there were spares in the box should you lose any.

frame_box_closed

I will scan and upload the instructions that come in the box as after a quick Google, I cannot immediatley find them online.

I found this helpful video online (see below), which I used in conjunction with the instructions that came in the box. Flicking back and forth between the two seemed to serve me well and it did not take too long to assemble the core components.

Watch the video (https://www.youtube.com/watch?v=4H4Mjw7wpys)

I think given the veracity of the instructions I have pointed you to (and my lack of taking photos throughout) there is not much need in me writing a comprehensive instruction set for this part of the process.

My only notes would be:

- Be extra careful of overtightening the motor mounts and stripping the holes
- Do not tighten any screws that you will be loosening very shortly to install other components
- The grub screws in the landing gear are particularly fiddly

One thing that I do not recall the video showing is the connection of the power connector to the PDB. This requires you to solder two relativley big solder joints.

XT60_pigtail_soldered

As you can see, red goes to the positive (+) and black goes to the negative (-).

> [!TIP]
> You can use the multimeter to check for continutity through your soldered joints. Make contact with one probe to the end of the XT60 connector and the other to the corresponding points on the PDB.

---

## CubePilot PowerBrick

This may or may not be the correct place for this information but as we currently do not have a power/battery section, this feel the most fitting. With the cube orange+, you get a power brick in the box which sits between the battery and PDB that is designed to tap off the power required to maintain the flight controller and its peripherals (i.e. things connected to the flight controller). There is a cable in the box that connects directly into the bottom of the power brick and goes into the power1 port on the cube orange+. As I am writing this ater the fact, in the image below the cable has already been threaded through the completed drone but I will add some photos so it is clearer about where it sits in the architecture. This will also be made clear in the [wiring diragram](/media/images/wiring_diagram.svg).

power_converters

➡️ [Continue to: ESCs >>](04-esc.md)

Some pictures I did take through the process that I have not used in the above descriptions...

frame_box_open
frame_box_component_bags2
frame_top_plate_and_arms
drone_on_desk_no_electronics

➡️ [Continue to: ESCs >>](04-esc.md)

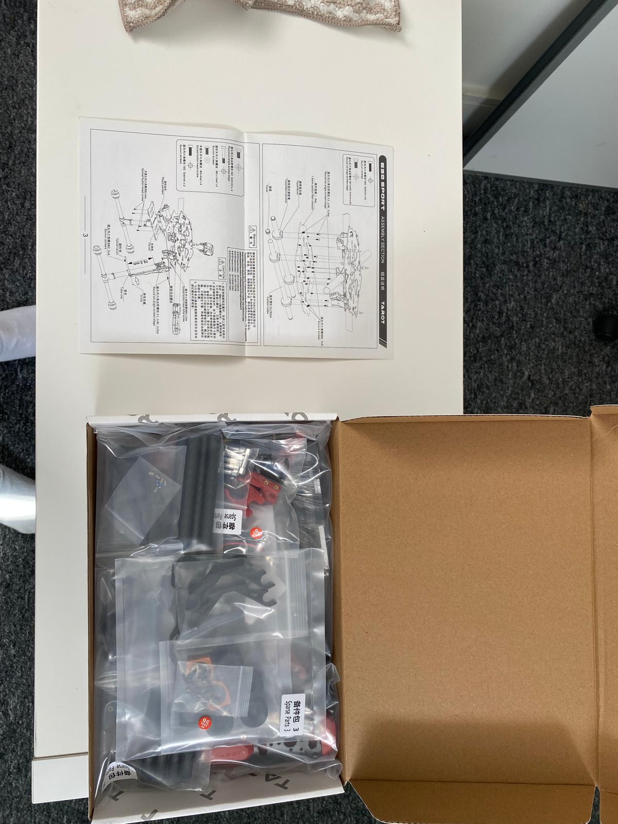
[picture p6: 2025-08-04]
media/images/frame_assembly/frame_box_open.jpg

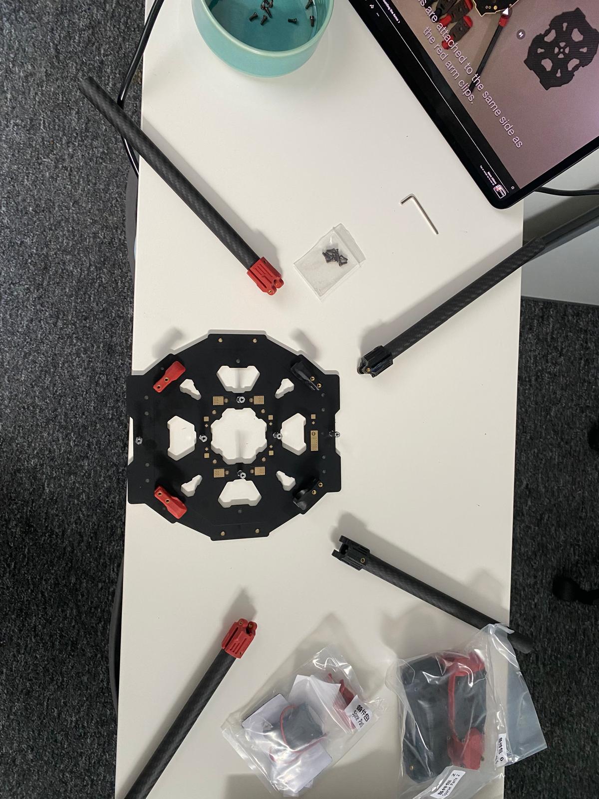
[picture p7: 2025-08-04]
media/images/frame_assembly/frame_top_plate_and_arms.jpg

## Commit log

2025-08-07 adding gps stand stl file repo
    [GPS_stand_v1.stl]
2025-08-11 shorter GPS stand
    v1 is kind of ridiculously tall...
    [GPS_stand_base_v2.stl]
2025-08-12 wiring diagram upload
    svg file format
